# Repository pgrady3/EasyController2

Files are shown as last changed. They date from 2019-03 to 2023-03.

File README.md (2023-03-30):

### The EasyController3 has been released. It is cheaper, more efficient, and uses parts that are in-stock. [Check it out here!](https://github.com/pgrady3/EasyController3)

# EasyController2

*NOTE: Check out the [EasyTelemetry](https://github.com/pgrady3/EasyTelemetry) project for a similarly simple board for logging vehicle voltage/current/speed/position.*

A simple brushless (BLDC) sensored motor controller. Intended to drive electric vehicles such as electric bikes, skateboards, or Eco-Marathon vehicles. The controller can handle nominal power of about 1kW.

This controller was designed to fill a gap in publicly released motor controller designs. It is simple enough to serve as an introduction to power electronics, and to hopefully allow those unfamiliar with motors to get their feet wet. To this end, the controller is designed to be as simple and easy-to-understand as possible. Thus it lacks more complex features such as sensorless control or current-feedback control, however these features can be easily added with some modifications. This project is meant as a learning tool and a foundation to potentially build more complex designs from.

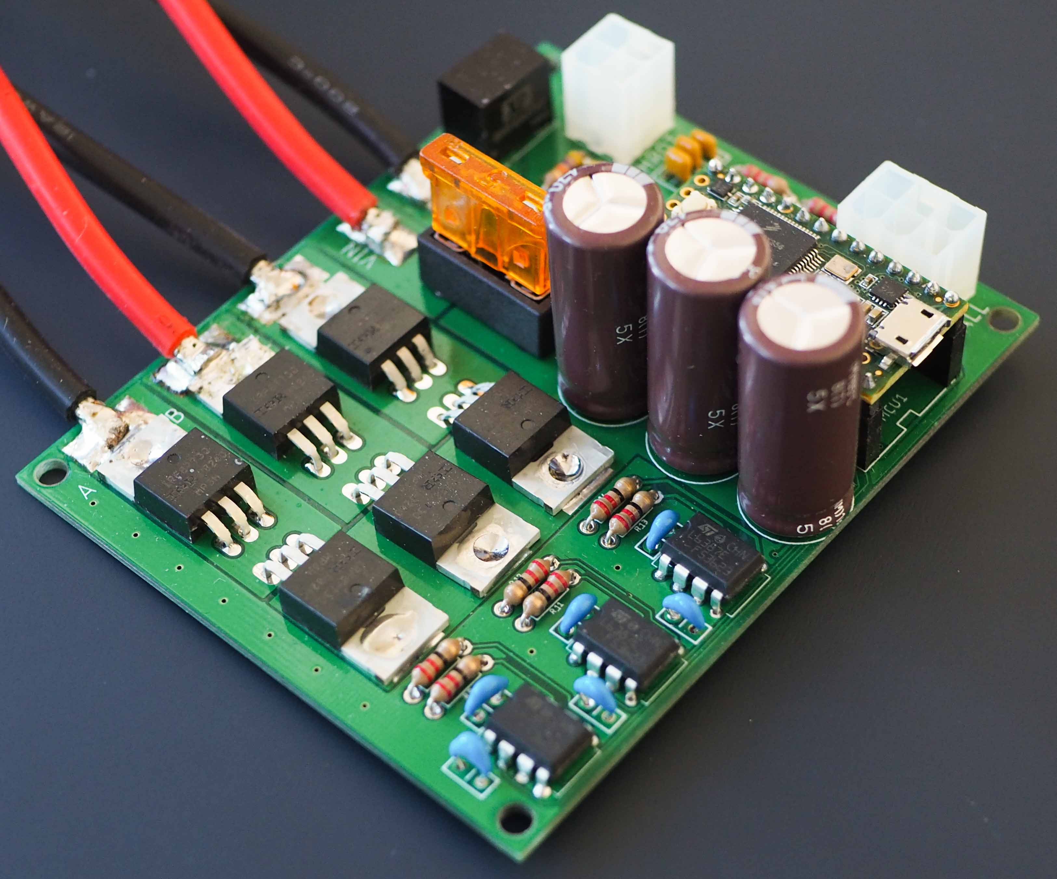
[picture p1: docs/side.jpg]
Assembled Controller


This project is a successor to the [2016 controller](http://www.duke-ev.org/blog/2016/11/27/the-2016-motor-controller) released on the DEV website. This design is dramatically easier to solder, more robust, and simpler, while still achieving the same functionality. We strongly encourage use of this new design.

## Specifications
* 15v-60v operation
* 20A continuous current, 40A burst (more with heatsinking)
* All through-hole design. Easy to solder!
* Socket for automotive fuse
* Automatic hall sensor identification
* Extremely simple code. <200 lines with comments
* Duty-cycle control
* Teensy 3.2 microcontroller
* L6387E gate drivers
* IRFB7730 MOSFETS
* BOM cost of 70 USD
* Totally open source

## Schematic

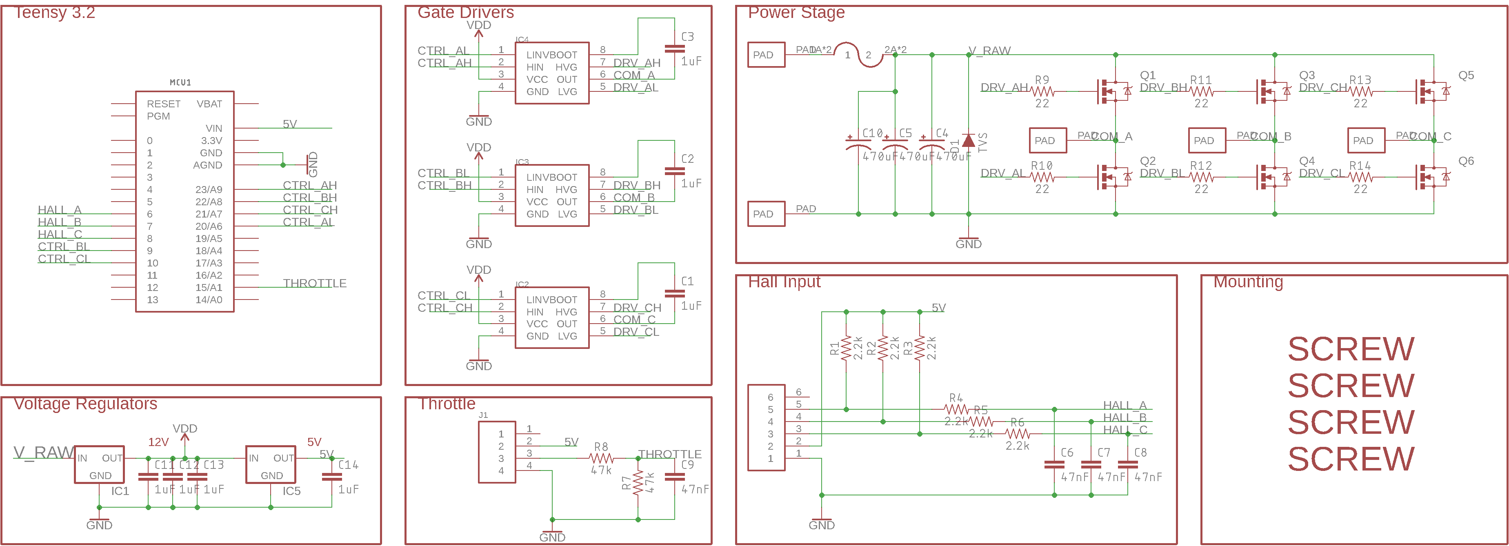
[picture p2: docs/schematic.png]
Schematic


## Board

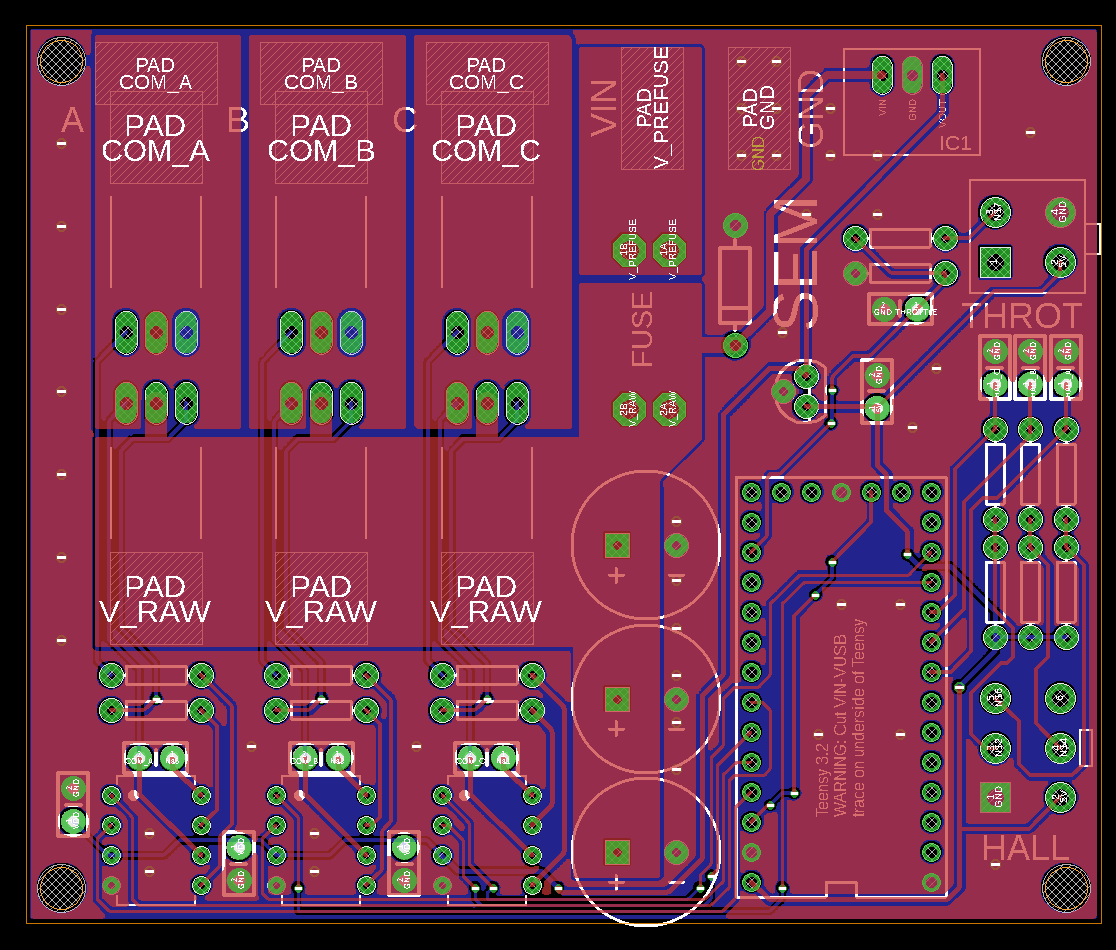
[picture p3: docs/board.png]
Board
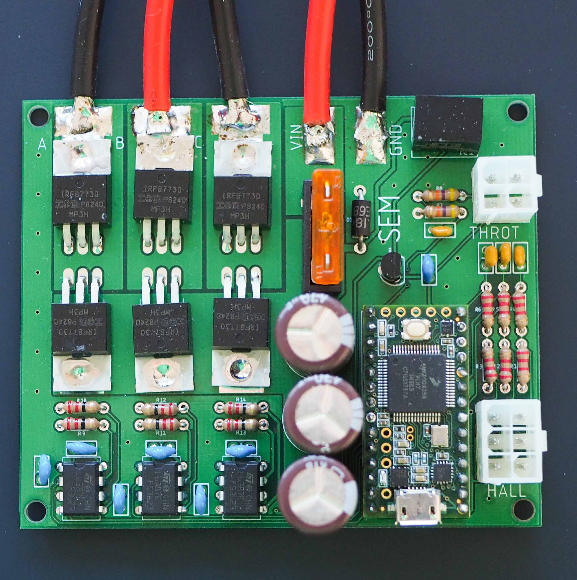
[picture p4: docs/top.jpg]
 

## Software Used

* PCB layout: [Eagle](https://www.autodesk.com/products/eagle/free-download)
* Compiler: [Arduino](https://www.arduino.cc/) with [PJRC Teensyduino add-on](https://www.pjrc.com/teensy/td_download.html)

## Assembly

This respository includes Gerber files which can be directly submitted to PCB manufacturers. We recommend Chinese manufacturers such as [AllPCB](https://www.allpcb.com/) or [JLCPCB](https://jlcpcb.com/). The repository also includes a Bill of Materials (BOM) with Digikey part numbers to order from.

Assembly is straightforward. However, it is recommended to cut the VIN-VUSB trace on the [underside of the Teensy](https://www.pjrc.com/teensy/card7b_rev1.pdf). Cutting the trace means that the Teensy can no longer be powered over USB. This is a safety procaution to prevent the controller feeding power backwards into your computer's USB port. 

## Design Improvements

The EasyController2 was designed with absolute simplicity in mind. It is meant to be as easy to understand as possible at the expense of additional features.

However, this design is very similar to the [world record motor controller](https://github.com/DukeElectricVehicles/dev-eagle/tree/master/Controller2019_Guinness) that powered DEV's vehicle [Eta to a Guinness World Record](https://pratt.duke.edu/about/news/duke-student-team-wins-second-guinness-world-record-vehicle-efficiency). Improvements to the world record design include:

* Lower quiescent power. The EasyController2 draws about 1 watt of quiescent power. As Eta's nomial power consumption was only 19 watts, this is too high. This can be improved with slower clocking of the microcontroller and more intelligent power supply design.
* Hybrid sensor/sensorless control. All electric vehicles need sensors for initial motor startup. However at high speed, hall sensors become noisy and do not provide as clean of trasitions as BEMF sensorless monitoring.
* Current feedback control. It is critical that the motor be run in the correct operating range to minimize resistance versus magnetic losses in the motor. This requires a current control loop, keeping the motor operating at the optimal power level.
* Synchronous switching. The EasyController2 only PWMs the high-side MOSFET, and in off times, the current flows through the low-side body diode. This is known as non-synchronous switching, and results in a roughly 0.7v loss during switch off-times. This loss becomes more significant at low duty cycles. Performing [synchronous switching](https://www.digikey.com/en/articles/techzone/2015/sep/what-you-need-to-know-about-synchronous-voltage-regulation) is only possible with current feedback control, and was thus omitted from the EasyController for simplicity. With synchronous switching and a current feedback loop, regen can be accomplished.

These improvements are only critical for those seeking to squeeze the last few percent of efficiency out of their powertrain. However, for most applications, the EasyController2 is more than sufficient. These improvements are left as an excercise to future electrical engineers to keep with the spirit of the Shell Eco-Marathon.

## Contact Us

This controller was designed by Patrick Grady from Duke Electric Vehicles. If you need help or clarification, please [send us a message on our website.](http://www.duke-ev.org/dev-contact-us)

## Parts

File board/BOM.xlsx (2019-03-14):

Digikey part # | Designator | Qty | Price | Description
497-6217-5-ND | IC2,IC3,IC4 | 3 | 1.66 | Gate driver | 4.98 | 70.75
445-173257-1-ND | C1,C2,C3,C11,C12,C13,C14 | 7 | 0.33 | 1uF cap | 2.31
IRFB7730PBF-ND | Q1,Q2,Q3,Q4,Q5,Q6 | 6 | 3.51 | NFET | 21.06
P6KE68CALFCT-ND | D1 | 1 | 0.47 | TVS Diode | 0.47
565-3994-ND | C4,C5,C10 | 3 | 1.15 | 470uF cap | 3.45
CF14JT2K20CT-ND | R1,R2,R3,R4,R5,R6 | 6 | 0.1 | 2.2k resistor | 0.6
BC1082CT-ND | C6,C7,C8,C9 | 3 | 0.16 | 47nF cap | 0.48
36-3557-2-ND | J3 | 1 | 1.03 | Fuse holder | 1.03
1470-4533-ND | IC1 | 1 | 8 | Voltage Regulator | 8
CF14JT47K0CT-ND | R7,R8 | 2 | 0.1 | 47k resistor | 0.2
1568-1231-ND | MCU1 | 1 | 22.5 | Teensy 3.2 | 22.5
CF14JT22R0CT-ND | R9,R10,R11,R12,R13,R14 | 6 | 0.1 | 22 ohm | 0.6
497-1184-1-ND | IC5 | 1 | 0.35 | 5V Linear reg | 0.35
S1012EC-14-ND |  | 2 | 0.31 | 14 pin male header | 0.62
S7012-ND |  | 2 | 0.91 | 14 pin female header | 1.82
A30603-ND | J1 | 1 | 0.68 | 4 pin female connector VAL-U-LOK | 0.68
A30604-ND | J2 | 1 | 0.65 | 6 pin female connector VAL-U-LOK | 0.65
A30591-ND |  | 1 | 0.21 | 4 pin male connector VAL-U-LOK | 0.21
A30592-ND |  | 1 | 0.24 | 6 pin male connector VAL-U-LOK | 0.24
A99267CT-ND |  | 10 | 0.05 | VAL-U-LOK crimp pin | 0.5
345-1092-ND‎ |  | 1 | 1.46 | Heatsink, optional
345-1006-ND |  | 1 | 3.82 | Thermal paste, for heatsink

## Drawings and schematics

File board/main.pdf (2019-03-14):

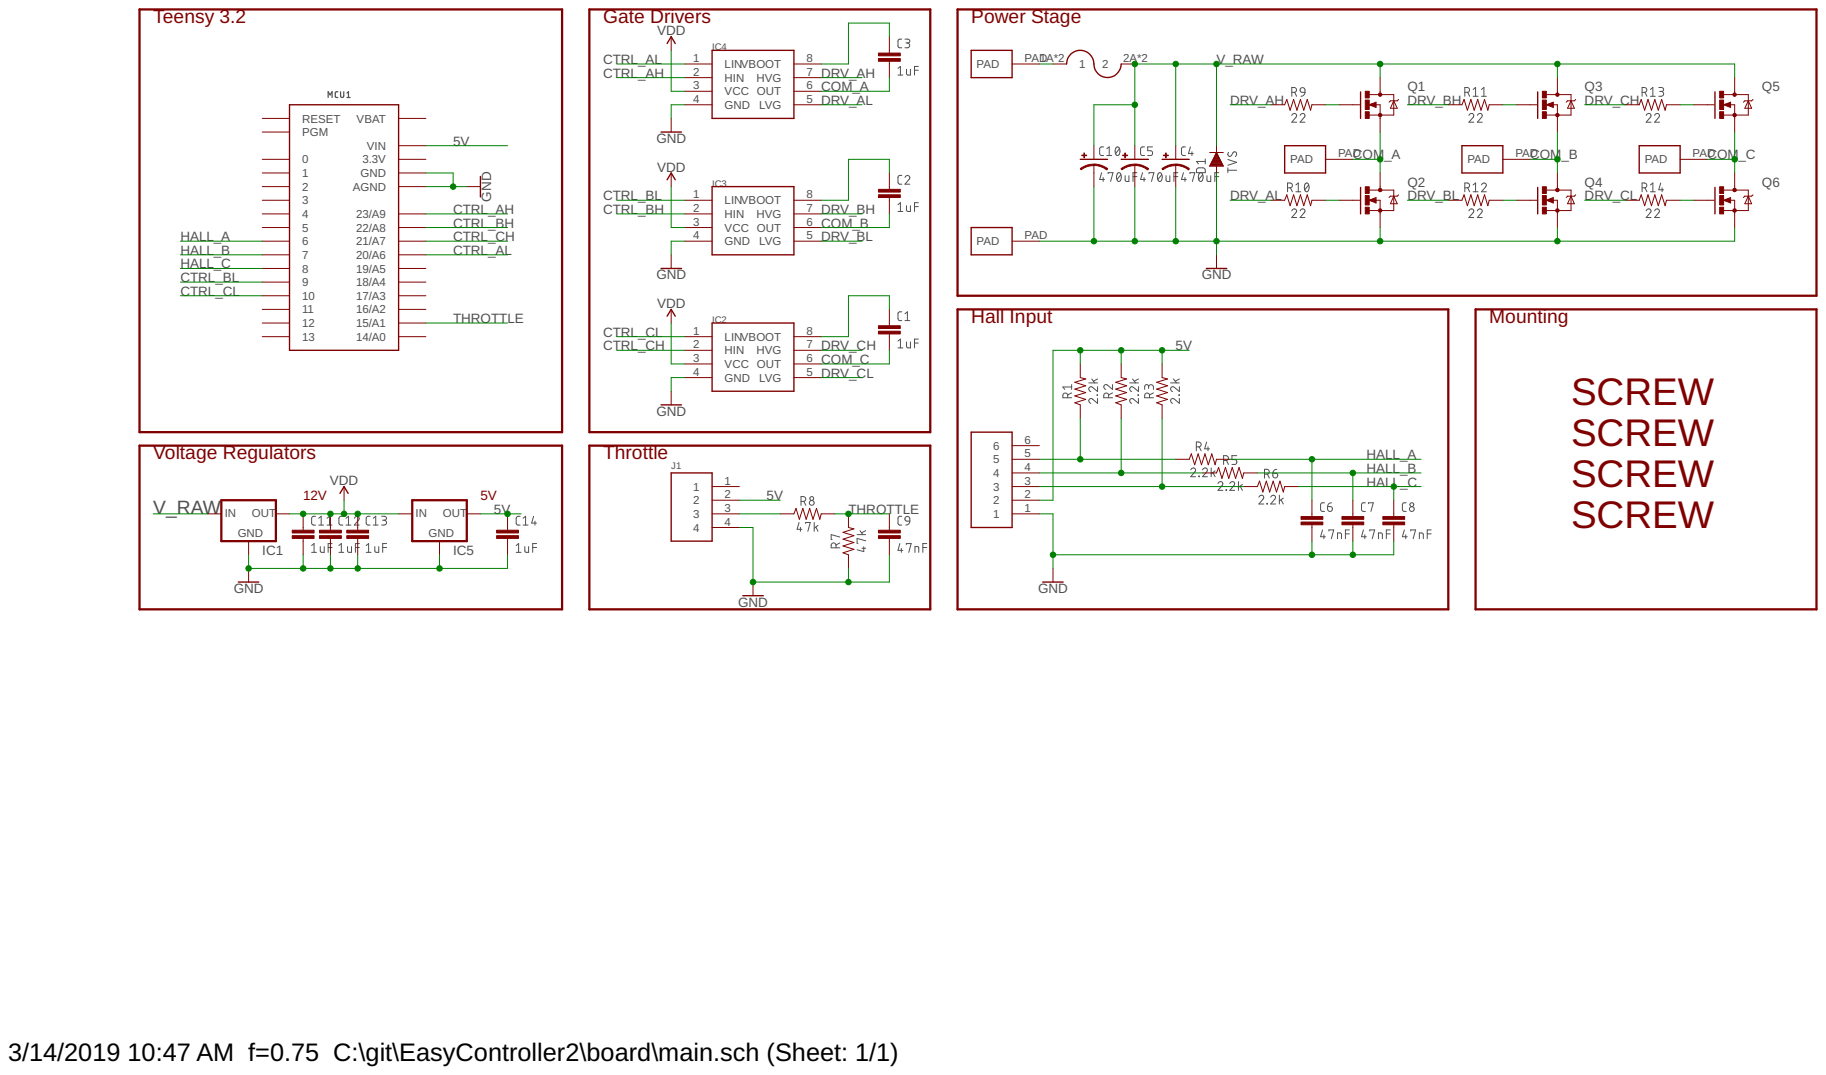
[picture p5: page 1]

3/14/2019 10:47 AM f=0.75 C:\git\EasyController2\board\main.sch (Sheet: 1/1)

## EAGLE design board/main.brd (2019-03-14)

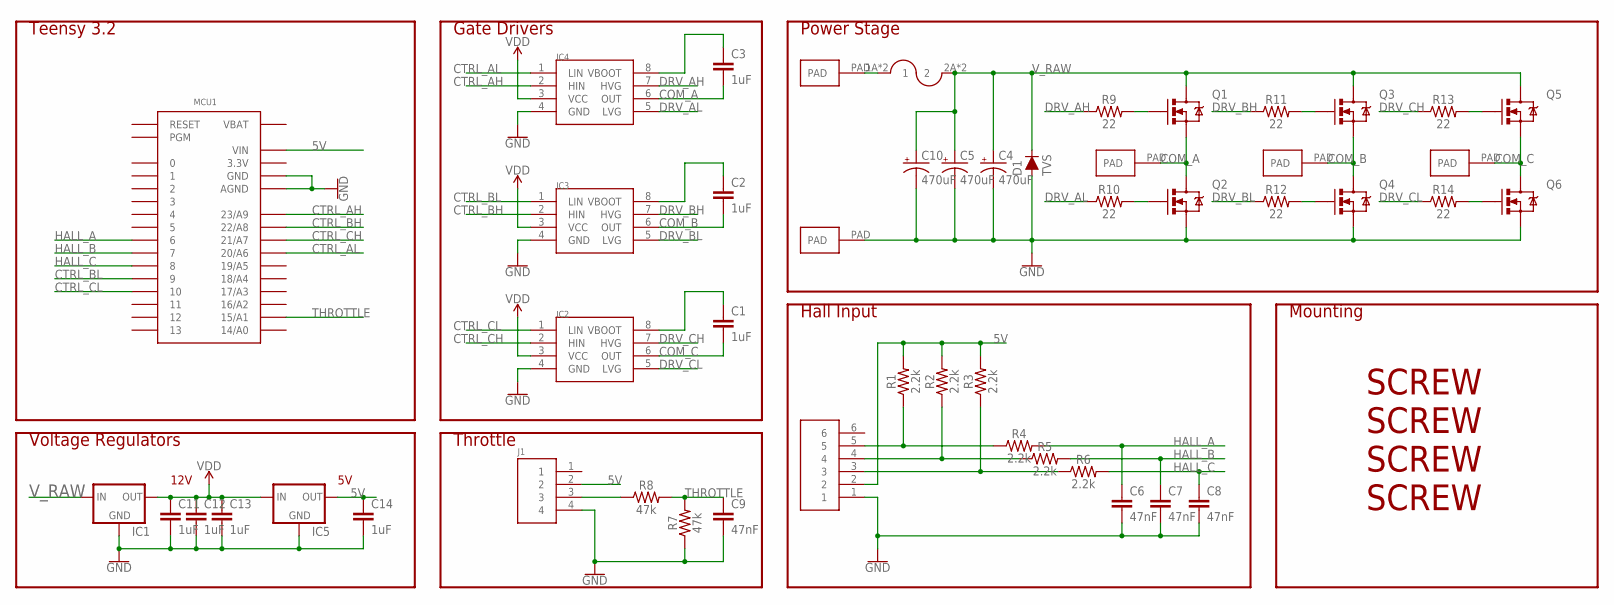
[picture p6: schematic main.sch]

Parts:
C1, C2, C3, C11, C12, C13, C14: 1uF; CAP-PTH-SMALL-KIT
C4, C5, C10: 470uF; CPOL-RADIAL-5MM-10MM
C6, C7, C8, C9: 47nF; CAP-PTH-SMALL-KIT
D1: TVS; DIODE-1N4001
IC1: V_REG_78XX; V78W_BACKWARDS
IC2, IC3, IC4: L6387EDIP8; DIP762W53P254L1092H508Q8B
IC5: V_REG_78XXTO-92_UNTESTED; TO-92
J1: HEADER4VALULOK; 4PINVALULOK
J2: HEADER6; 6PINVALULOK
J3: FUSE; AUTO_FUSE
MCU1: TEENSY_3.0_BASIC
Q1, Q2, Q3, Q4, Q5, Q6: MOSFET-NCHANNELTO-220-FLAT; TO-220-FLAT
R1, R2, R3, R4, R5, R6: 2.2k; AXIAL-0.3
R7, R8: 47k; AXIAL-0.3
R9, R10, R11, R12, R13, R14: 22; AXIAL-0.3
U$4, U$5, U$6, U$7, U$8: PAD
U$10, U$11, U$12, U$13: SCREW; M3HOLE

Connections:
3.3V: MCU1.3.3V, MCU1.3.3V1 (3.3V)
5V: C14.1, IC5.1 (OUT), J1.2, J2.2, MCU1.VIN, R1.P$2 (2), R2.P$2 (2), R3.P$2 (2)
COM_A: C3.2, IC4.6 (OUT), Q1.3 (S), Q2.2 (D), Q2.PAD (D), U$6.PAD
COM_B: C2.2, IC3.6 (OUT), Q3.3 (S), Q4.2 (D), Q4.PAD (D), U$7.PAD
COM_C: C1.2, IC2.6 (OUT), Q5.3 (S), Q6.2 (D), Q6.PAD (D), U$8.PAD
CTRL_AH: IC4.2 (HIN), MCU1.23/A9
CTRL_AL: IC4.1 (LIN), MCU1.20/A6
CTRL_BH: IC3.2 (HIN), MCU1.22/A8
CTRL_BL: IC3.1 (LIN), MCU1.9
CTRL_CH: IC2.2 (HIN), MCU1.21/A7
CTRL_CL: IC2.1 (LIN), MCU1.10
DRV_AH: IC4.7 (HVG), R9.P$1 (1)
DRV_AL: IC4.5 (LVG), R10.P$1 (1)
DRV_BH: IC3.7 (HVG), R11.P$1 (1)
DRV_BL: IC3.5 (LVG), R12.P$1 (1)
DRV_CH: IC2.7 (HVG), R13.P$1 (1)
DRV_CL: IC2.5 (LVG), R14.P$1 (1)
GND: C4.-, C5.-, C6.2, C7.2, C8.2, C9.2, C10.-, C11.2, C12.2, C13.2, C14.2, D1.A, IC1.GND, IC2.4 (GND), IC3.4 (GND), IC4.4 (GND), IC5.2 (GND), J1.4, J2.1, MCU1.AGND, MCU1.GND, MCU1.GND1 (GND), Q2.3 (S), Q4.3 (S), Q6.3 (S), R7.P$1 (1), U$5.PAD
HALL_A: C6.1, MCU1.6, R4.P$2 (2)
HALL_B: C7.1, MCU1.7, R5.P$2 (2)
HALL_C: C8.1, MCU1.8, R6.P$2 (2)
unnamed: C1.1, IC2.8 (VBOOT)
unnamed: J2.3, R3.P$1 (1), R6.P$1 (1)
unnamed: C2.1, IC3.8 (VBOOT)
unnamed: J2.4, R2.P$1 (1), R5.P$1 (1)
unnamed: C3.1, IC4.8 (VBOOT)
unnamed: J2.5, R1.P$1 (1), R4.P$1 (1)
unnamed: J1.3, R8.P$1 (1)
unnamed: Q1.1 (G), R9.P$2 (2)
unnamed: Q2.1 (G), R10.P$2 (2)
unnamed: Q3.1 (G), R11.P$2 (2)
unnamed: Q4.1 (G), R12.P$2 (2)
unnamed: Q5.1 (G), R13.P$2 (2)
unnamed: Q6.1 (G), R14.P$2 (2)
THROTTLE: C9.1, MCU1.15/A1, R7.P$2 (2), R8.P$2 (2)
VBAT: MCU1.VBAT
VDD: C11.1, C12.1, C13.1, IC1.OUT, IC2.3 (VCC), IC3.3 (VCC), IC4.3 (VCC), IC5.3 (IN)
V_PREFUSE: J3.1A (1), J3.1B (1), U$4.PAD
V_RAW: C4.+, C5.+, C10.+, D1.C, IC1.IN, J3.2A (2), J3.2B (2), Q1.2 (D), Q1.PAD (D), Q3.2 (D), Q3.PAD (D), Q5.2 (D), Q5.PAD (D)

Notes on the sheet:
Power Stage
Hall Input
Gate Drivers
Throttle
Teensy 3.2
Voltage Regulators
12V
Mounting

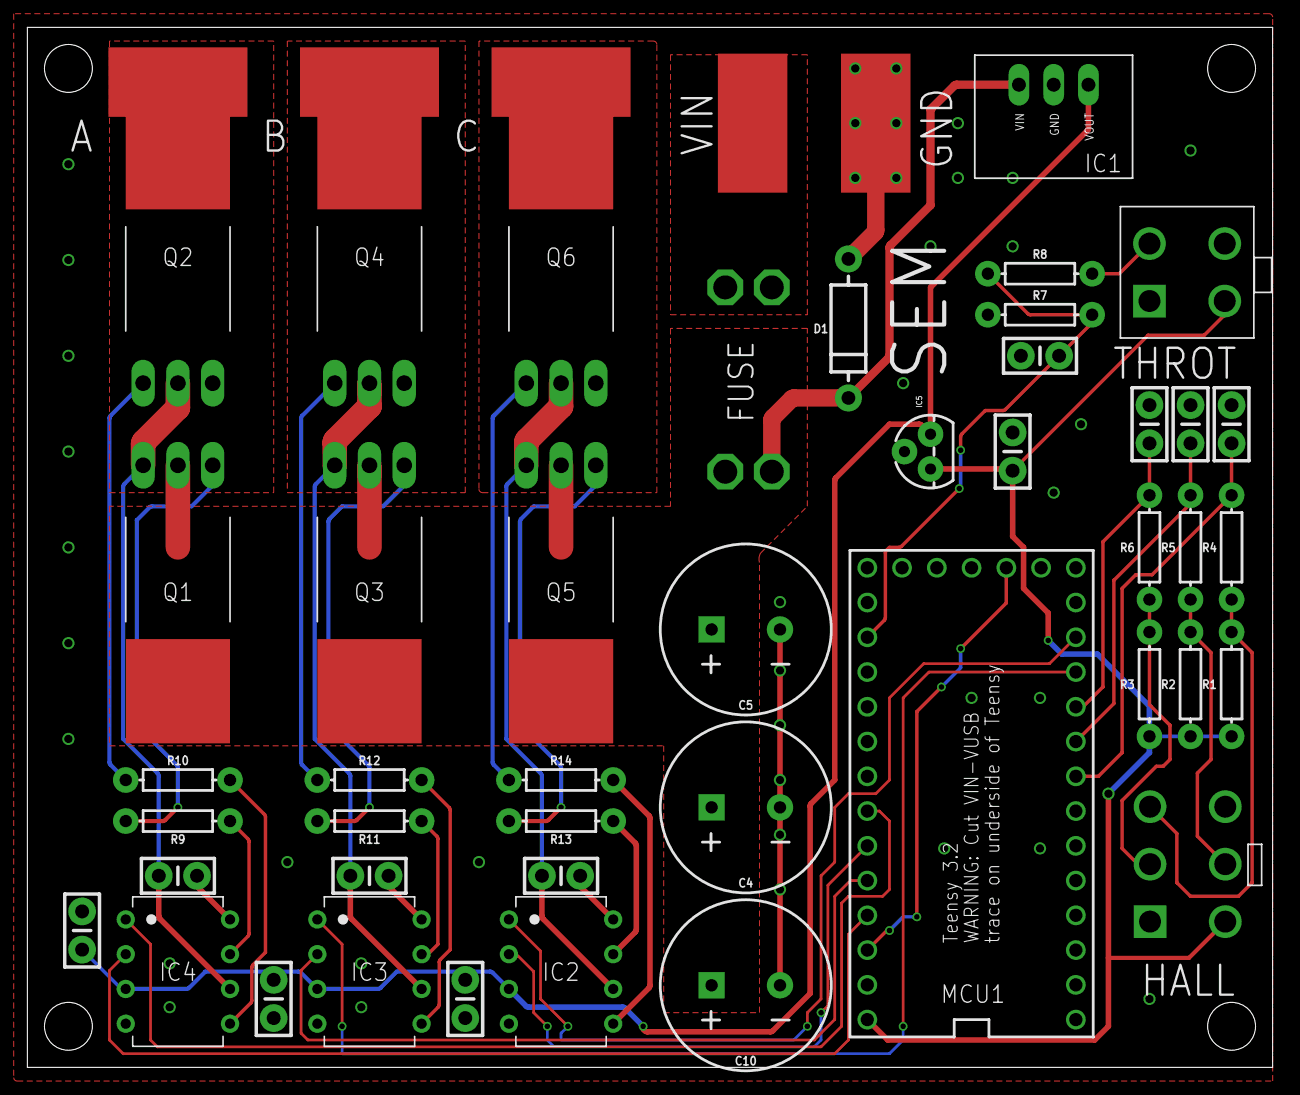
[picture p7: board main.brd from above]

Board: 2 copper layers, 91.0 x 76.0 mm, 53 parts (0 on the bottom side), 38 nets.

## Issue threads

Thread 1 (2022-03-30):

motor wiring question

technicalpyro, 2022-03-30:
i see from your images the motor wiring connection to the drivers is black red black could you please elaborate on what that should be connected to on the motor i have but this board and it does seem to work but it locks up when i apply throttle and eventually trigers the BMS over current limit on my power source

any help is appreciated

Regards,
Sean

technicalpyro, 2022-03-30:
i have solved my issue was something completely unrelated

Closed 2022-03-30.

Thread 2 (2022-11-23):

Circuit diagram and how program controller IC

Kamalkant1234, 2022-11-23:
Kindly share circuit diagram and how will do program controller IC wirth Arduino-IDE.

pgrady3, 2022-12-13:
The circuit diagram is available under docs/schematic.png

The Teensy 3.2 getting started guide shows how to upload code and install the Teensyduino plugin into Arduino. [https://www.pjrc.com/teensy/first_use.html](https://www.pjrc.com/teensy/first_use.html)

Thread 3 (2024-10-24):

Can I use Esp32 as micro controller

ToastedAvenger, 2024-10-24:
As the question mentions i want to ask if i can use esp32 instead of teensy. What problems can i face by changing the controller?

ToastedAvenger, 2024-10-28:
Can anyone please provide me some info on this query?

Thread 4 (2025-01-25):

Completely unsuitable component!

Remmert1, 2025-01-25:
Guys!... When you post a miracle regulator, look into the tech doc. High-voltage driver L6387ED - it won't work at all.
**High level logic threshold voltage - min 3.6V**
No development board produces a high signal greater than 3.3v. Neither ESP32, nor Teensy, nor Nano

And I'm a deer... I bought drivers and only then checked...(((((

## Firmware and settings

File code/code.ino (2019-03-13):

#define THROTTLE_PIN 15       // Throttle pin
#define THROTTLE_LOW 150      // These LOW and HIGH values are used to scale the ADC reading. More on this below
#define THROTTLE_HIGH 710

#define HALL_1_PIN 6
#define HALL_2_PIN 7
#define HALL_3_PIN 8

#define AH_PIN 23             // Pins from the Teensy to the gate drivers. AH = A high, etc
#define AL_PIN 20
#define BH_PIN 22
#define BL_PIN 9
#define CH_PIN 21
#define CL_PIN 10

#define LED_PIN 13            // The teensy has a built-in LED on pin 13

#define HALL_OVERSAMPLE 4     // Hall oversampling count. More on this in the getHalls() function

uint8_t hallToMotor[8] = {255, 255, 255, 255, 255, 255, 255, 255};

void setup() {                // The setup function is called ONCE on boot-up
  Serial.begin(115200);

  pinMode(LED_PIN, OUTPUT);
  digitalWriteFast(LED_PIN, HIGH);

  pinMode(AH_PIN, OUTPUT);    // Set all PWM pins as output
  pinMode(AL_PIN, OUTPUT);
  pinMode(BH_PIN, OUTPUT);
  pinMode(BL_PIN, OUTPUT);
  pinMode(CH_PIN, OUTPUT);
  pinMode(CL_PIN, OUTPUT);

  analogWriteFrequency(AH_PIN, 8000); // Set the PWM frequency. Since all pins are on the same timer, this sets PWM freq for all

  pinMode(HALL_1_PIN, INPUT);         // Set the hall pins as input
  pinMode(HALL_2_PIN, INPUT);
  pinMode(HALL_3_PIN, INPUT);

  pinMode(THROTTLE_PIN, INPUT);
  
  identifyHalls();                  // Uncomment this if you want the controller to auto-identify the hall states at startup!
}

void loop() {                         // The loop function is called repeatedly, once setup() is done
  
  uint8_t throttle = readThrottle();  // readThrottle() is slow. So do the more important things 200 times more often
  for(uint8_t i = 0; i < 200; i++)
  {  
    uint8_t hall = getHalls();              // Read from the hall sensors
    uint8_t motorState = hallToMotor[hall]; // Convert from hall values (from 1 to 6) to motor state values (from 0 to 5) in the correct order. This line is magic
    writePWM(motorState, throttle);         // Actually command the transistors to switch into specified sequence and PWM value
  }
}

/* Magic function to do hall auto-identification. Moves the motor to all 6 states, then reads the hall values from each one
 * 
 * Note, that in order to get a clean hall reading, we actually need to commutate to half-states. So instead of going to state 3, for example
 * we commutate to state 3.5, by rapidly switching between states 3 and 4. After waiting for a while (half a second), we read the hall value.
 * Finally, print it
 */

void identifyHalls()
{
  for(uint8_t i = 0; i < 6; i++)
  {
    uint8_t nextState = (i + 1) % 6;        // Calculate what the next state should be. This is for switching into half-states
    Serial.print("Going to ");
    Serial.println(i);
    for(uint16_t j = 0; j < 200; j++)       // For a while, repeatedly switch between states
    {
      delay(1);
      writePWM(i, 20);
      delay(1);
      writePWM(nextState, 20);
    }
    hallToMotor[getHalls()] = (i + 2) % 6;  // Store the hall state - motor state correlation. Notice that +2 indicates 90 degrees ahead, as we're at half states
  }
  
  writePWM(0, 0);                           // Turn phases off
  
  for(uint8_t i = 0; i < 8; i++)            // Print out the array
  {
    Serial.print(hallToMotor[i]);
    Serial.print(", ");
  }
  Serial.println();
}

/* This function takes a motorState (from 0 to 5) as an input, and decides which transistors to turn on
 * dutyCycle is from 0-255, and sets the PWM value.
 * 
 * Note if dutyCycle is zero, or if there's an invalid motorState, then it turns all transistors off
 */

void writePWM(uint8_t motorState, uint8_t dutyCycle)
{
  if(dutyCycle == 0)                          // If zero throttle, turn all off
    motorState = 255;

  if(motorState == 0)                         // LOW A, HIGH B
      writePhases(0, dutyCycle, 0, 1, 0, 0);
  else if(motorState == 1)                    // LOW A, HIGH C
      writePhases(0, 0, dutyCycle, 1, 0, 0);
  else if(motorState == 2)                    // LOW B, HIGH C
      writePhases(0, 0, dutyCycle, 0, 1, 0);
  else if(motorState == 3)                    // LOW B, HIGH A
      writePhases(dutyCycle, 0, 0, 0, 1, 0);
  else if(motorState == 4)                    // LOW C, HIGH A
      writePhases(dutyCycle, 0, 0, 0, 0, 1);
  else if(motorState == 5)                    // LOW C, HIGH B
      writePhases(0, dutyCycle, 0, 0, 0, 1);
  else                                        // All off
      writePhases(0, 0, 0, 0, 0, 0);
}

/* Helper function to actually write values to transistors. For the low sides, takes a 0 or 1 for on/off
 * For high sides, takes 0-255 for PWM value
 */

void writePhases(uint8_t ah, uint8_t bh, uint8_t ch, uint8_t al, uint8_t bl, uint8_t cl)
{
  analogWrite(AH_PIN, ah);
  analogWrite(BH_PIN, bh);
  analogWrite(CH_PIN, ch);
  digitalWriteFast(AL_PIN, al);
  digitalWriteFast(BL_PIN, bl);
  digitalWriteFast(CL_PIN, cl);
}

/* Read hall sensors WITH oversamping. This is required, as the hall sensor readings are often noisy.
 * This function reads the sensors multiple times (defined by HALL_OVERSAMPLE) and only sets the output
 * to a 1 if a majority of the readings are 1. This really helps reject noise. If the motor starts "cogging" or "skipping"
 * at low speed and high torque, try increasing the HALL_OVERSAMPLE value
 * 
 * Outputs a number, with the last 3 binary digits corresponding to hall readings. Thus 0 to 7, or 1 to 6 in normal operation
 */

uint8_t getHalls()
{
  uint8_t hallCounts[] = {0, 0, 0};
  for(uint8_t i = 0; i < HALL_OVERSAMPLE; i++) // Read all the hall pins repeatedly, tally results 
  {
    hallCounts[0] += digitalReadFast(HALL_1_PIN);
    hallCounts[1] += digitalReadFast(HALL_2_PIN);
    hallCounts[2] += digitalReadFast(HALL_3_PIN);
  }

  uint8_t hall = 0;
  
  if (hallCounts[0] >= HALL_OVERSAMPLE / 2)     // If votes >= threshold, call that a 1
    hall |= (1<<0);                             // Store a 1 in the 0th bit
  if (hallCounts[1] >= HALL_OVERSAMPLE / 2)
    hall |= (1<<1);                             // Store a 1 in the 1st bit
  if (hallCounts[2] >= HALL_OVERSAMPLE / 2)
    hall |= (1<<2);                             // Store a 1 in the 2nd bit

  return hall & 0x7;                            // Just to make sure we didn't do anything stupid, set the maximum output value to 7
}

/* Read the throttle value from the ADC. Because our ADC can read from 0v-3.3v, but the throttle doesn't output over this whole range,
 * scale the throttle reading to take up the full range of 0-255
 */

uint8_t readThrottle()
{
  int32_t adc = analogRead(THROTTLE_PIN); // Note, analogRead can be slow!
  adc = (adc - THROTTLE_LOW) << 8;
  adc = adc / (THROTTLE_HIGH - THROTTLE_LOW);

  if (adc > 255) // Bound the output between 0 and 255
    return 255;

  if (adc < 0)
    return 0;
  
  return adc;
}

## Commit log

2019-03-13 Initial commit. Copied from controller 1_1
    [BOM.xlsx, main.brd, main.sch]
2019-03-13 Flipped connectors, changed silkscreen
    [main.brd]
2019-03-13 Changed names and silkscreen
    [main.brd]
2019-03-13 AllPCB submit for CNS
    [main.brd]
2019-03-14 Added connectors to BOM
    [BOM.xlsx, main.brd, main.sch]
2019-03-14 Added schematic PDF

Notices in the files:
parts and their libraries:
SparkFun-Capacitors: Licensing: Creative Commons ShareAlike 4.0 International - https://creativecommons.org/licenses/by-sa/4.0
